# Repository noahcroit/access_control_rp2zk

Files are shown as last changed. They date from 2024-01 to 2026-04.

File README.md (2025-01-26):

# Access Control Project
The project consists of <br>
- PCB design and the firmware of `Fail-Secure` door lock for the access control room. <br>
- Python worker of access control interface. This software will interract with the room management system later <br>

The project has 2 different version, v2023 and v2024.

## v2023 version
This version was focused on Proof-of-Concept and do a rapid prototype with both HW and SW. Micropython was used for the firmware development in RP2040 as for the Doorlock controller\
ZkTeco's access control was being used in this phase.

## v2024 version (the current ver.) 
PCB design with KiCAD for the doorlock controller. Hikvision's access control is being used in this phase instead of ZkTeco's.

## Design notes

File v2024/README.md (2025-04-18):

# FailSecureDoor_RP2 version 2 (2024)
The room consists of slider automatic door which needs the fail-secure bolt-lock system when outage occured. <br>
KiCAD is used for the controller board design (in `kicad`) and RPi Pico C SDK framework is used for the firmware development (in `firmware`). <br>
By the dafault, each door has the access control device `DS-K1T105AM` installed alongside. <br>
Our access control software will used the Software Worker (in `worker`) to interface with `DS-K1T105AM` via `ISAPI` and fail-secure board via MQTT. <br>
<br>
### Hardware Diagram
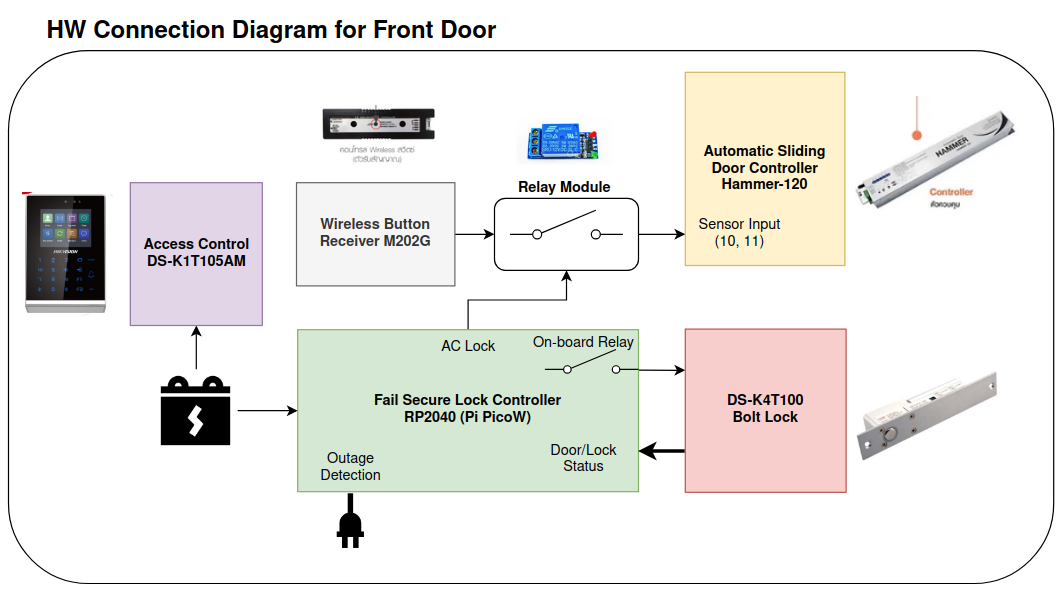
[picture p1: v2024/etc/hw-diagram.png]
 <br>
### Network Diagram
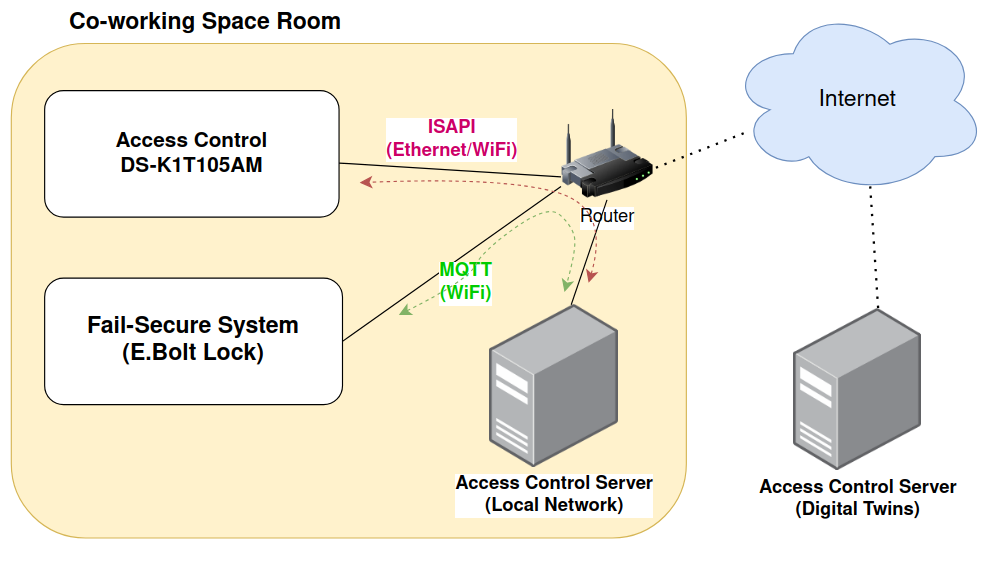
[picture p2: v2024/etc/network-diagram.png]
 <br>

### HW Installation
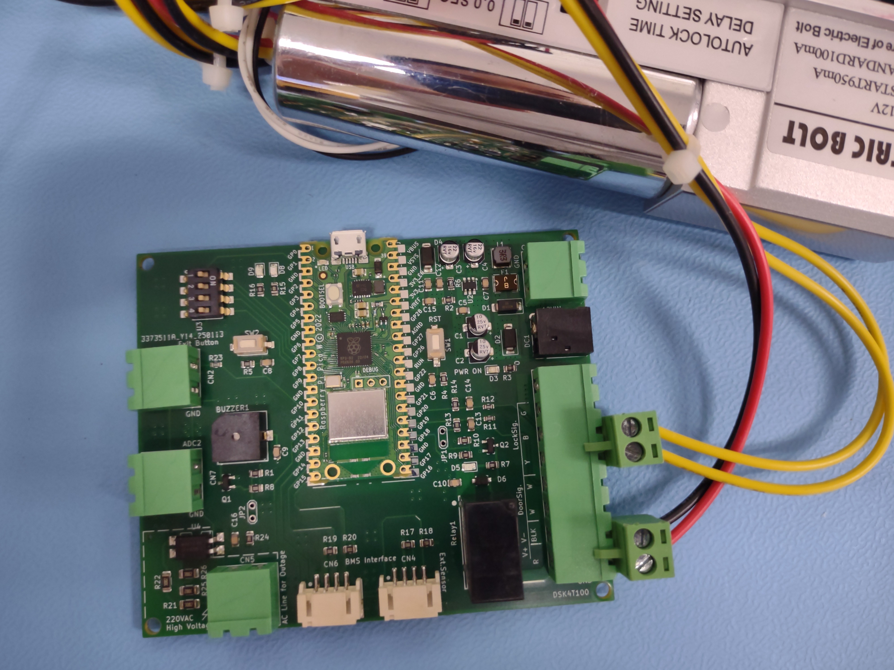
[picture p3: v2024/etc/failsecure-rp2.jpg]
 <br>
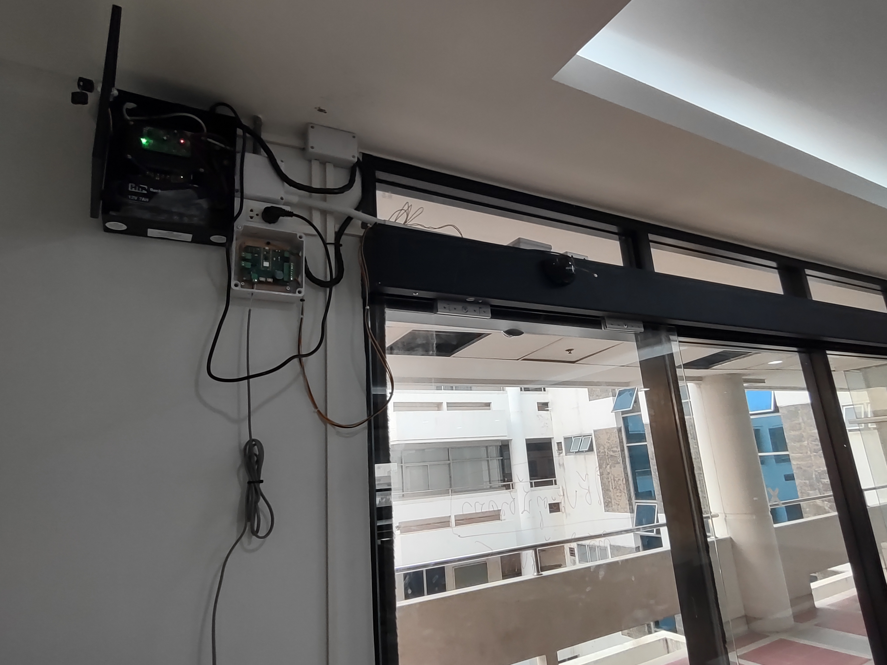
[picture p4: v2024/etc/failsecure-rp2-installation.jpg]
 <br>
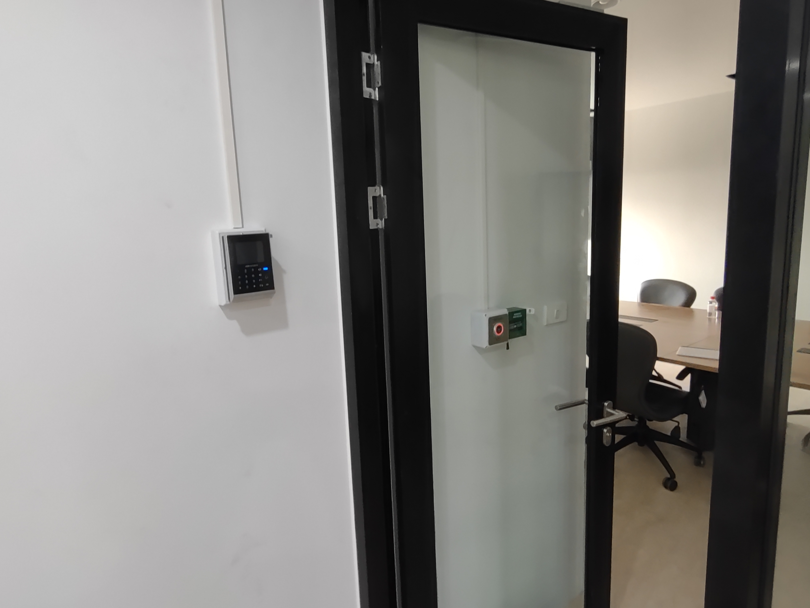
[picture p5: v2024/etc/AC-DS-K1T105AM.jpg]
 <br>

### Worker
To build the image <br>
```
cd worker
docker build -t acworker2024-image .
```

To run the worker as container <br>
```
docker run --network host -d --restart always --name acworker acworker2024-image
```

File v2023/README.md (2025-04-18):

# FailSecureDoor_RP2 version 1 (2023)
Firmware for Fail-secure door controller of access control room. It activates when power outage is occured. <br>
This is the rapid prototype project, PCB is constructed in a prototype way and Micropython are being used to develop the firmware. <br>
The access control unit is from ZkTeco brand. `pyzk` project is used for the python module to interface with ZkTeco AC. <br>
The project can be found in here https://github.com/fananimi/pyzk

### Fail-Secure Door Controller with Pico W (RP2040)
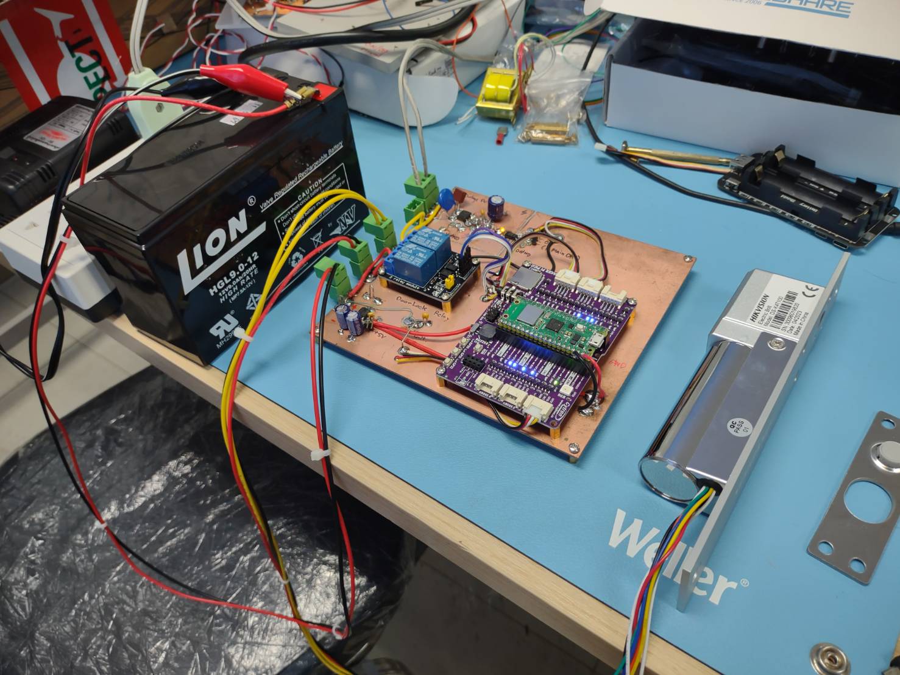
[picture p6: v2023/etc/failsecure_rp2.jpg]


The firmware is written in micropython, stored in folder `rp2`. `ampy` can be used to upload the codes to MCU.
To upload firmware.
1. Upload micropython firmware .uf2 of Pico W. The latest firmware can be founded in here
    https://micropython.org/download/RPI_PICO_W/
2. `cd` to the repo
```
cd access_control_rpzk
cd rp2
```
3. Run `ampy put` to put the network configuration .json file into MCU
```
ampy -p /dev/ttyACM0 network_config.json
```
4. Run `ampy put` to put the codes into MCU
```
ampy -p /dev/ttyACM0 put umqtt 
ampy -p /dev/ttyACM0 put main.py main.py q_scheduler.py secure_doorlock.py
```
5. Verify the upload files by `ampy ls` or `ampy get`
```
ampy -p /dev/ttyACM0 ls
```
6. Reset MCU and run it.

### Worker for ZKTeco's Access Control & FailSecure Door
To deploy using Docker
1. `cd` to the repo
```
cd access_control_rpzk
```
2. Build worker image
```
sudo docker build -t acworker-image .
```
3. Run container from built image
```
sudo docker run -d --network=host --name=acworker acworker-image
```

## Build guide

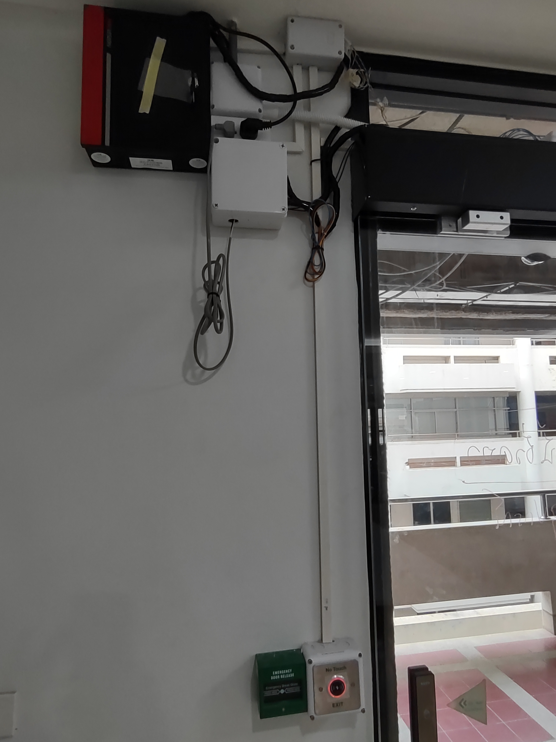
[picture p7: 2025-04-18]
v2024/etc/failsecure-rp2-installation-2.jpg

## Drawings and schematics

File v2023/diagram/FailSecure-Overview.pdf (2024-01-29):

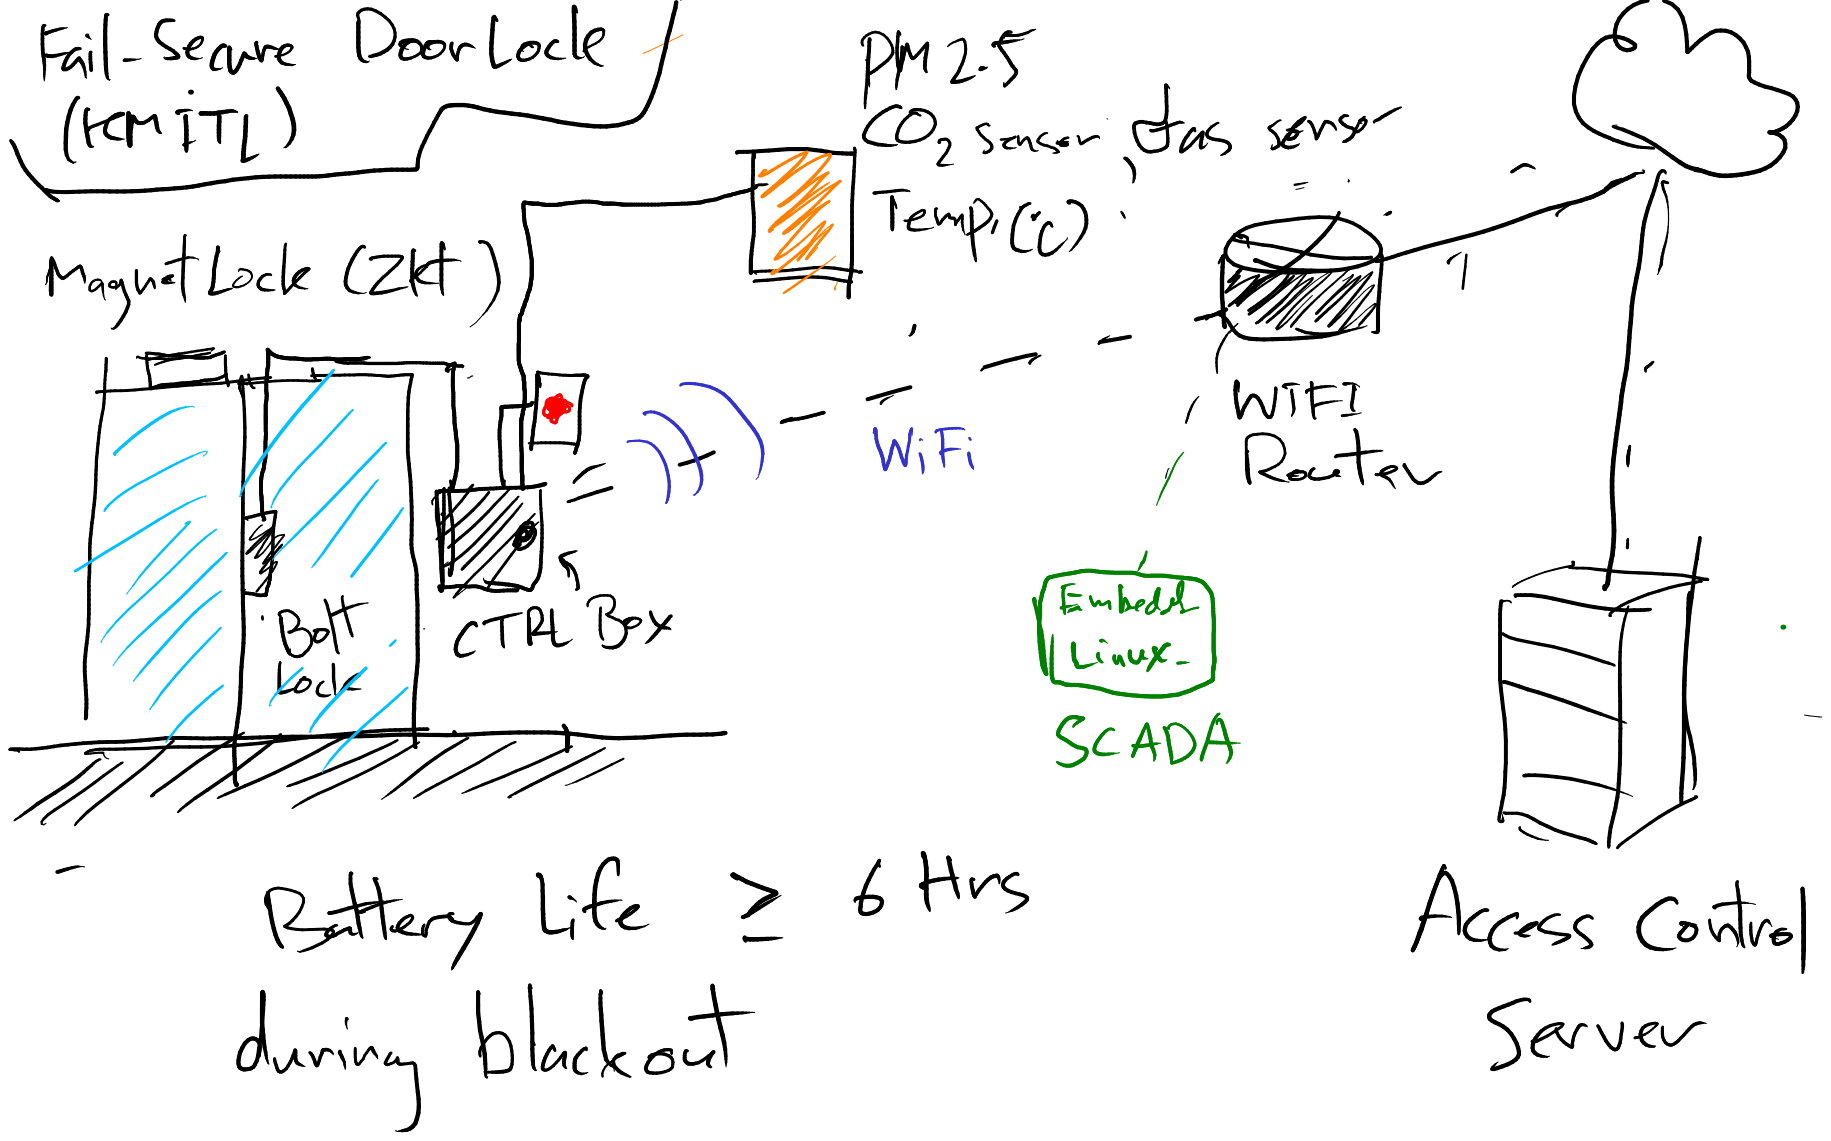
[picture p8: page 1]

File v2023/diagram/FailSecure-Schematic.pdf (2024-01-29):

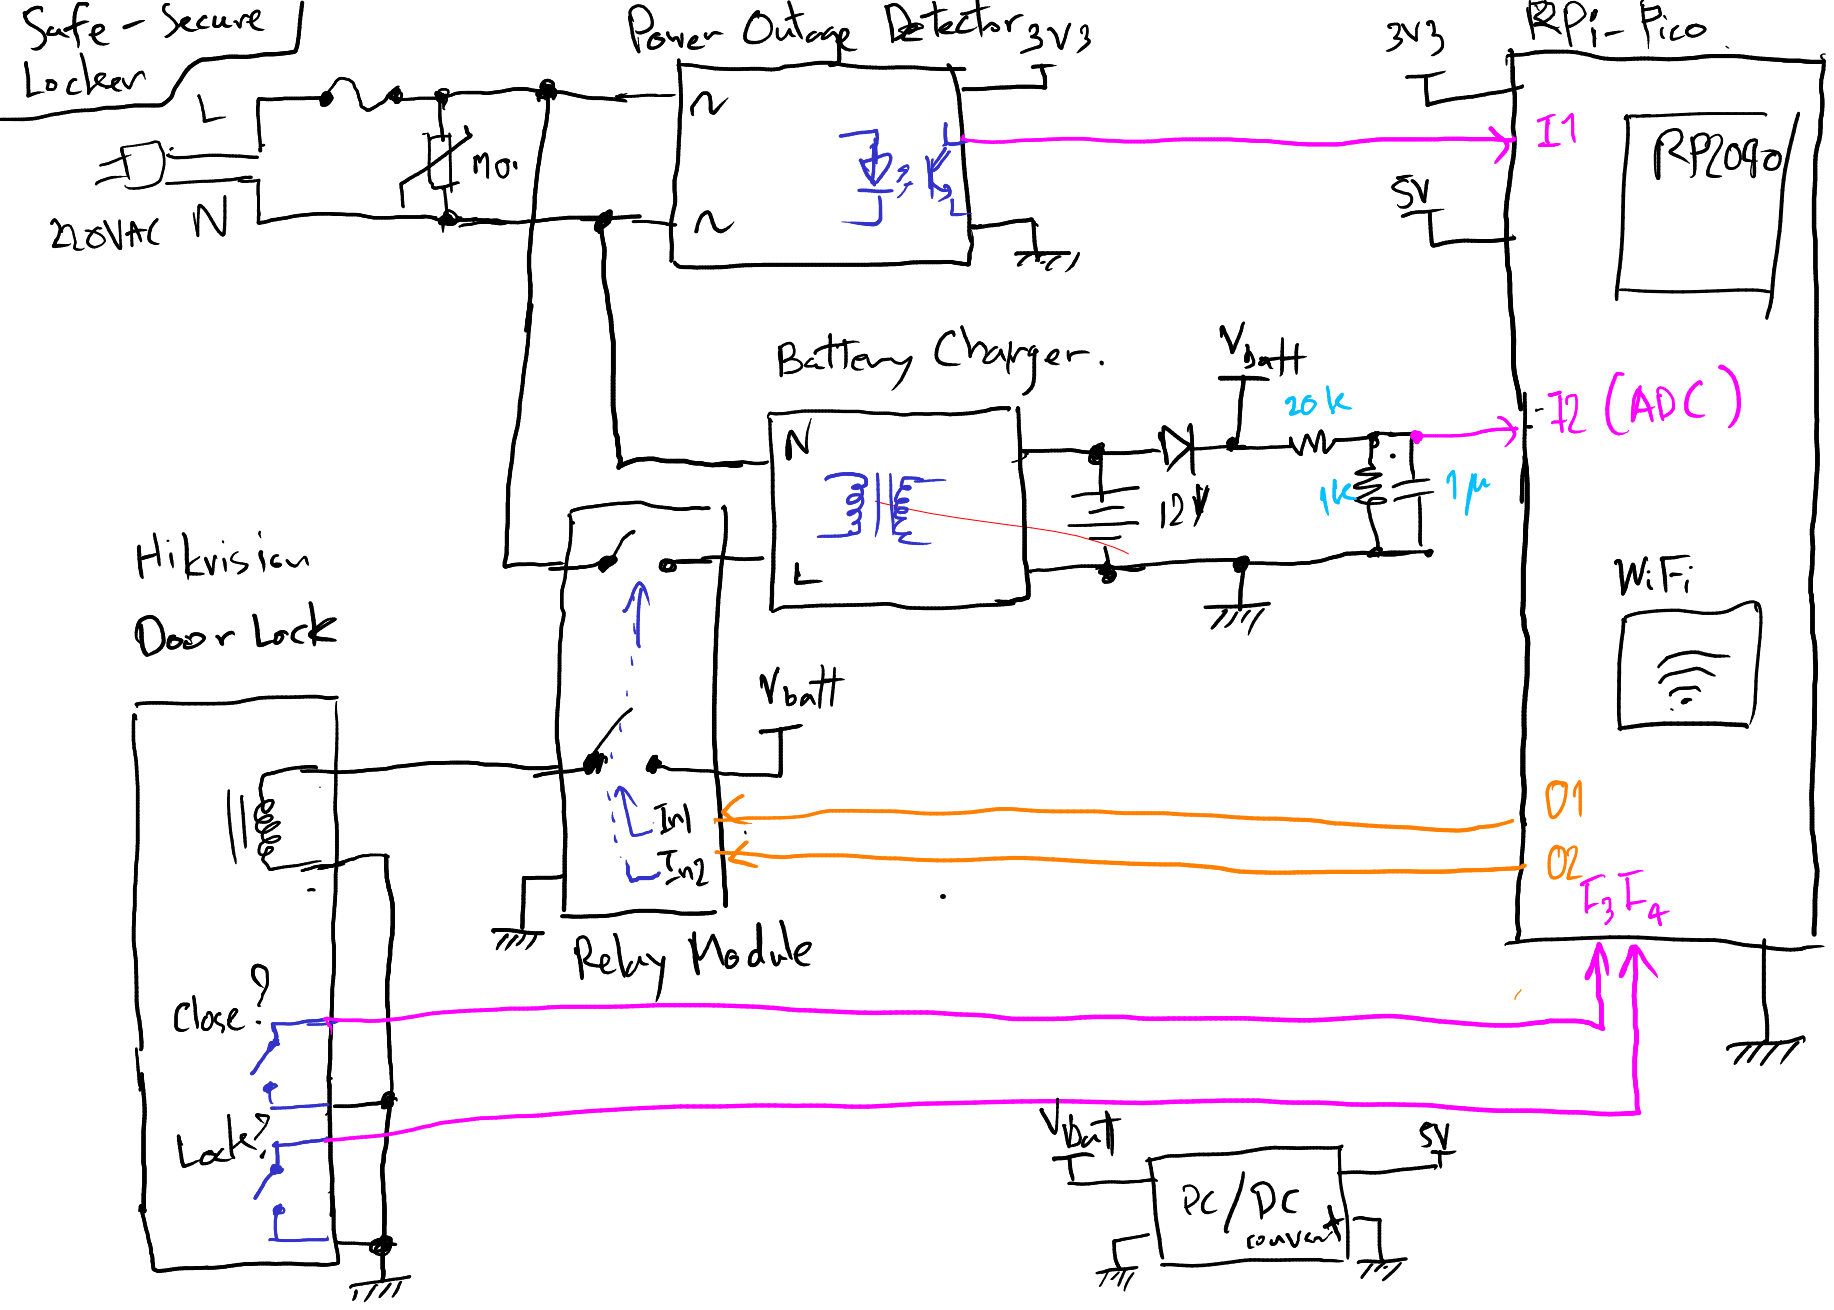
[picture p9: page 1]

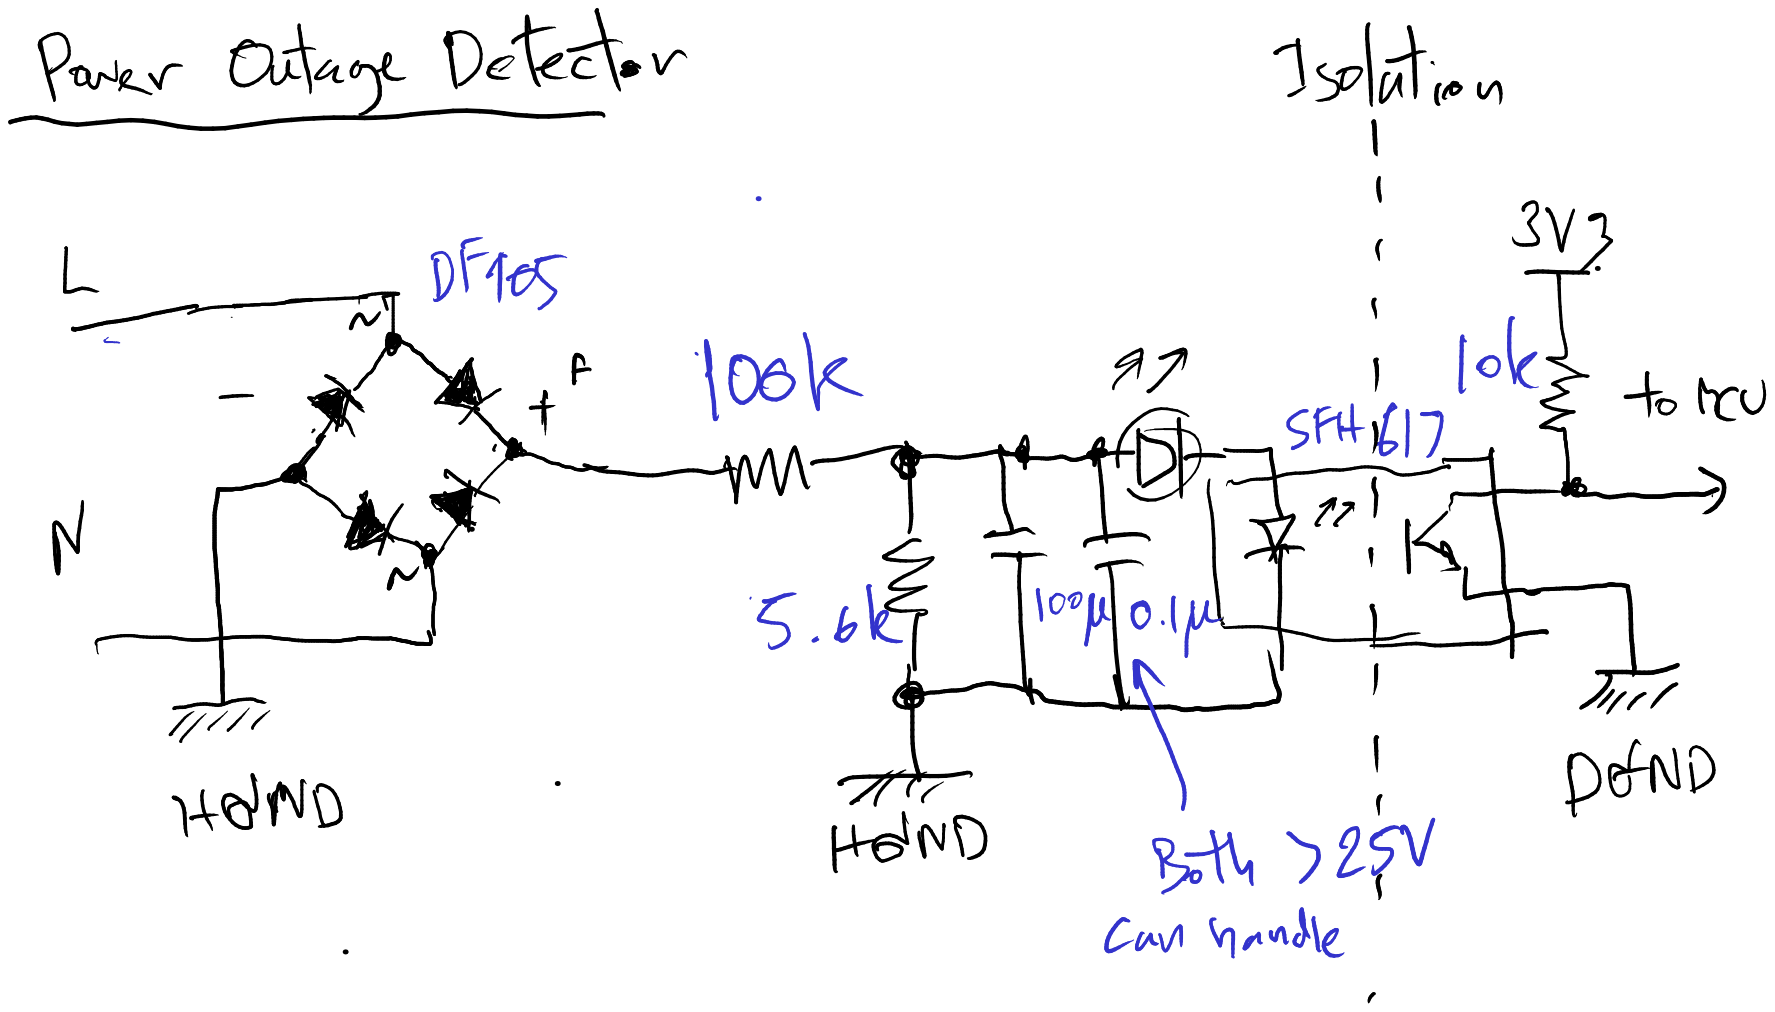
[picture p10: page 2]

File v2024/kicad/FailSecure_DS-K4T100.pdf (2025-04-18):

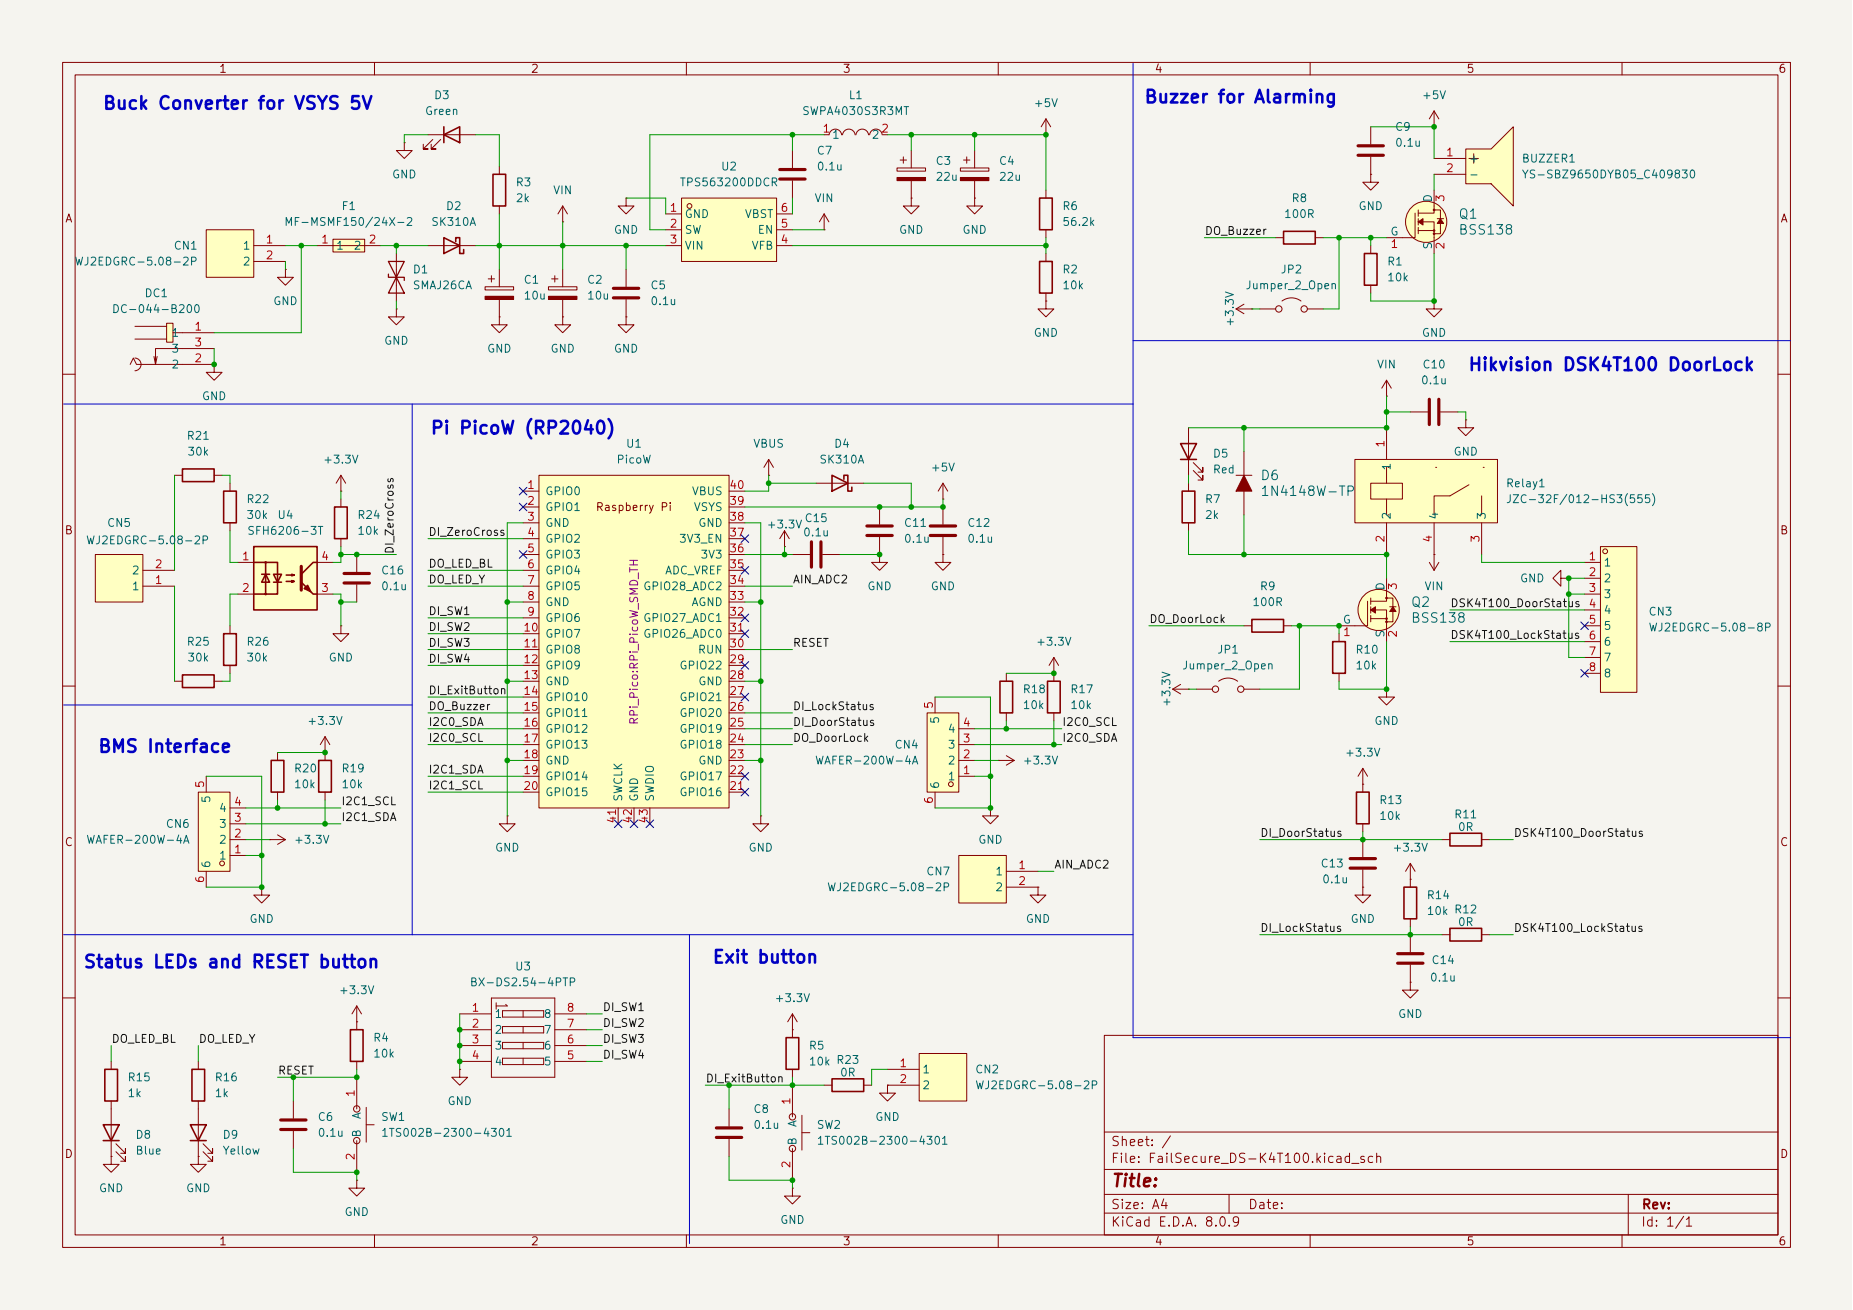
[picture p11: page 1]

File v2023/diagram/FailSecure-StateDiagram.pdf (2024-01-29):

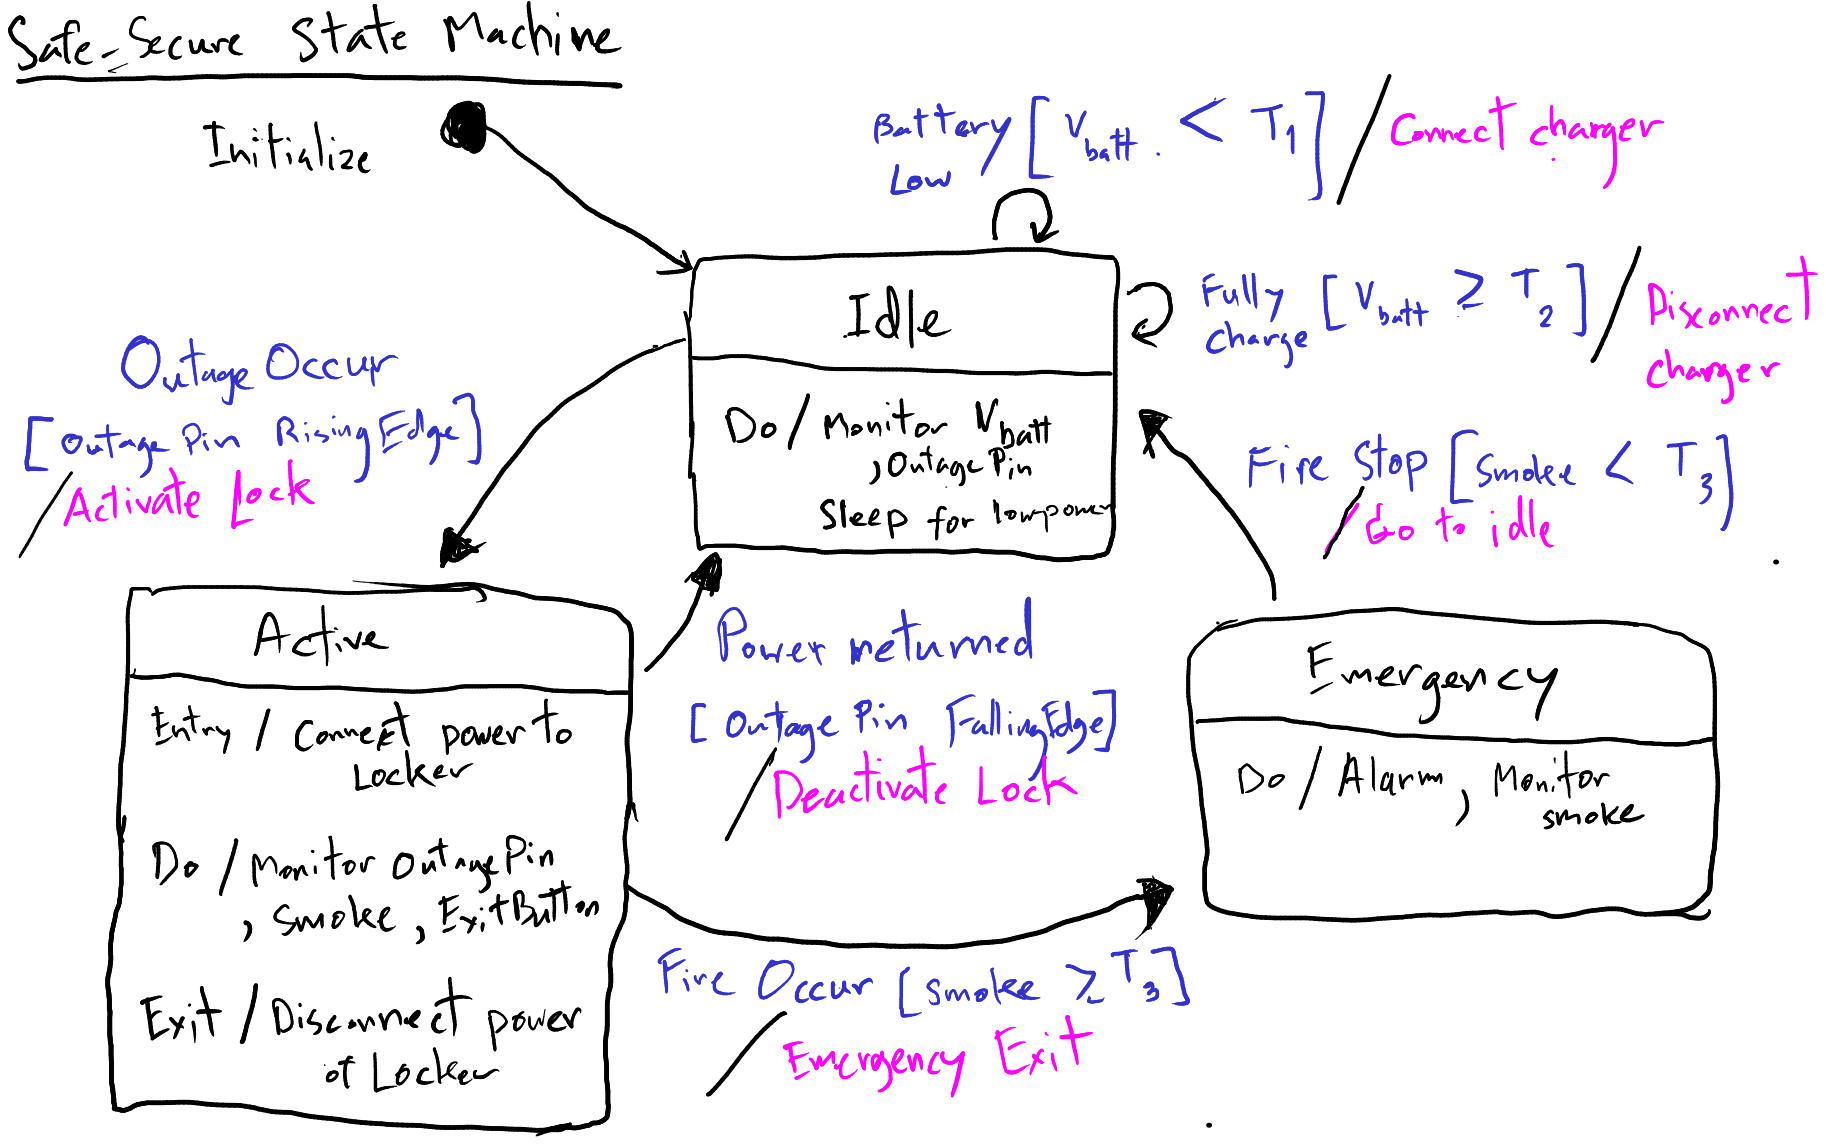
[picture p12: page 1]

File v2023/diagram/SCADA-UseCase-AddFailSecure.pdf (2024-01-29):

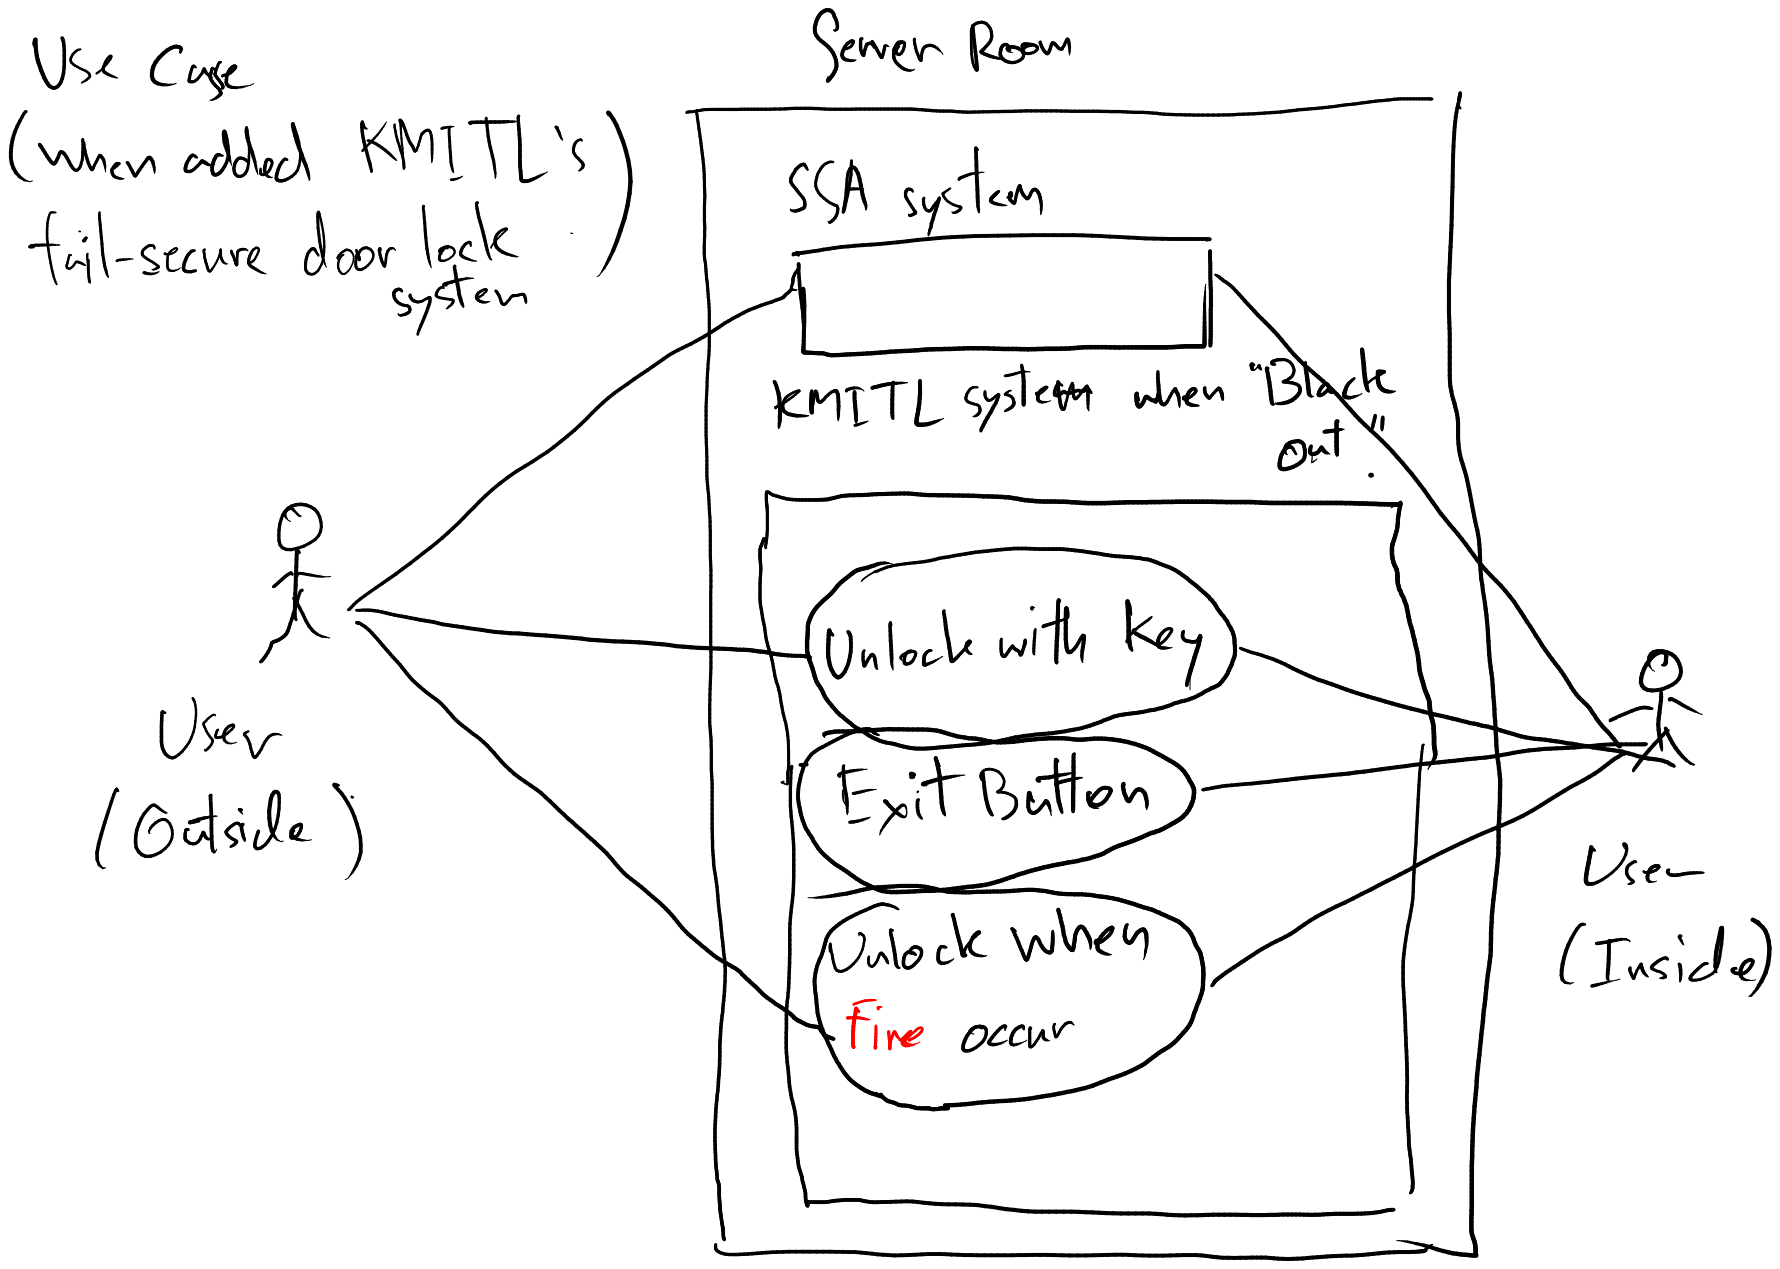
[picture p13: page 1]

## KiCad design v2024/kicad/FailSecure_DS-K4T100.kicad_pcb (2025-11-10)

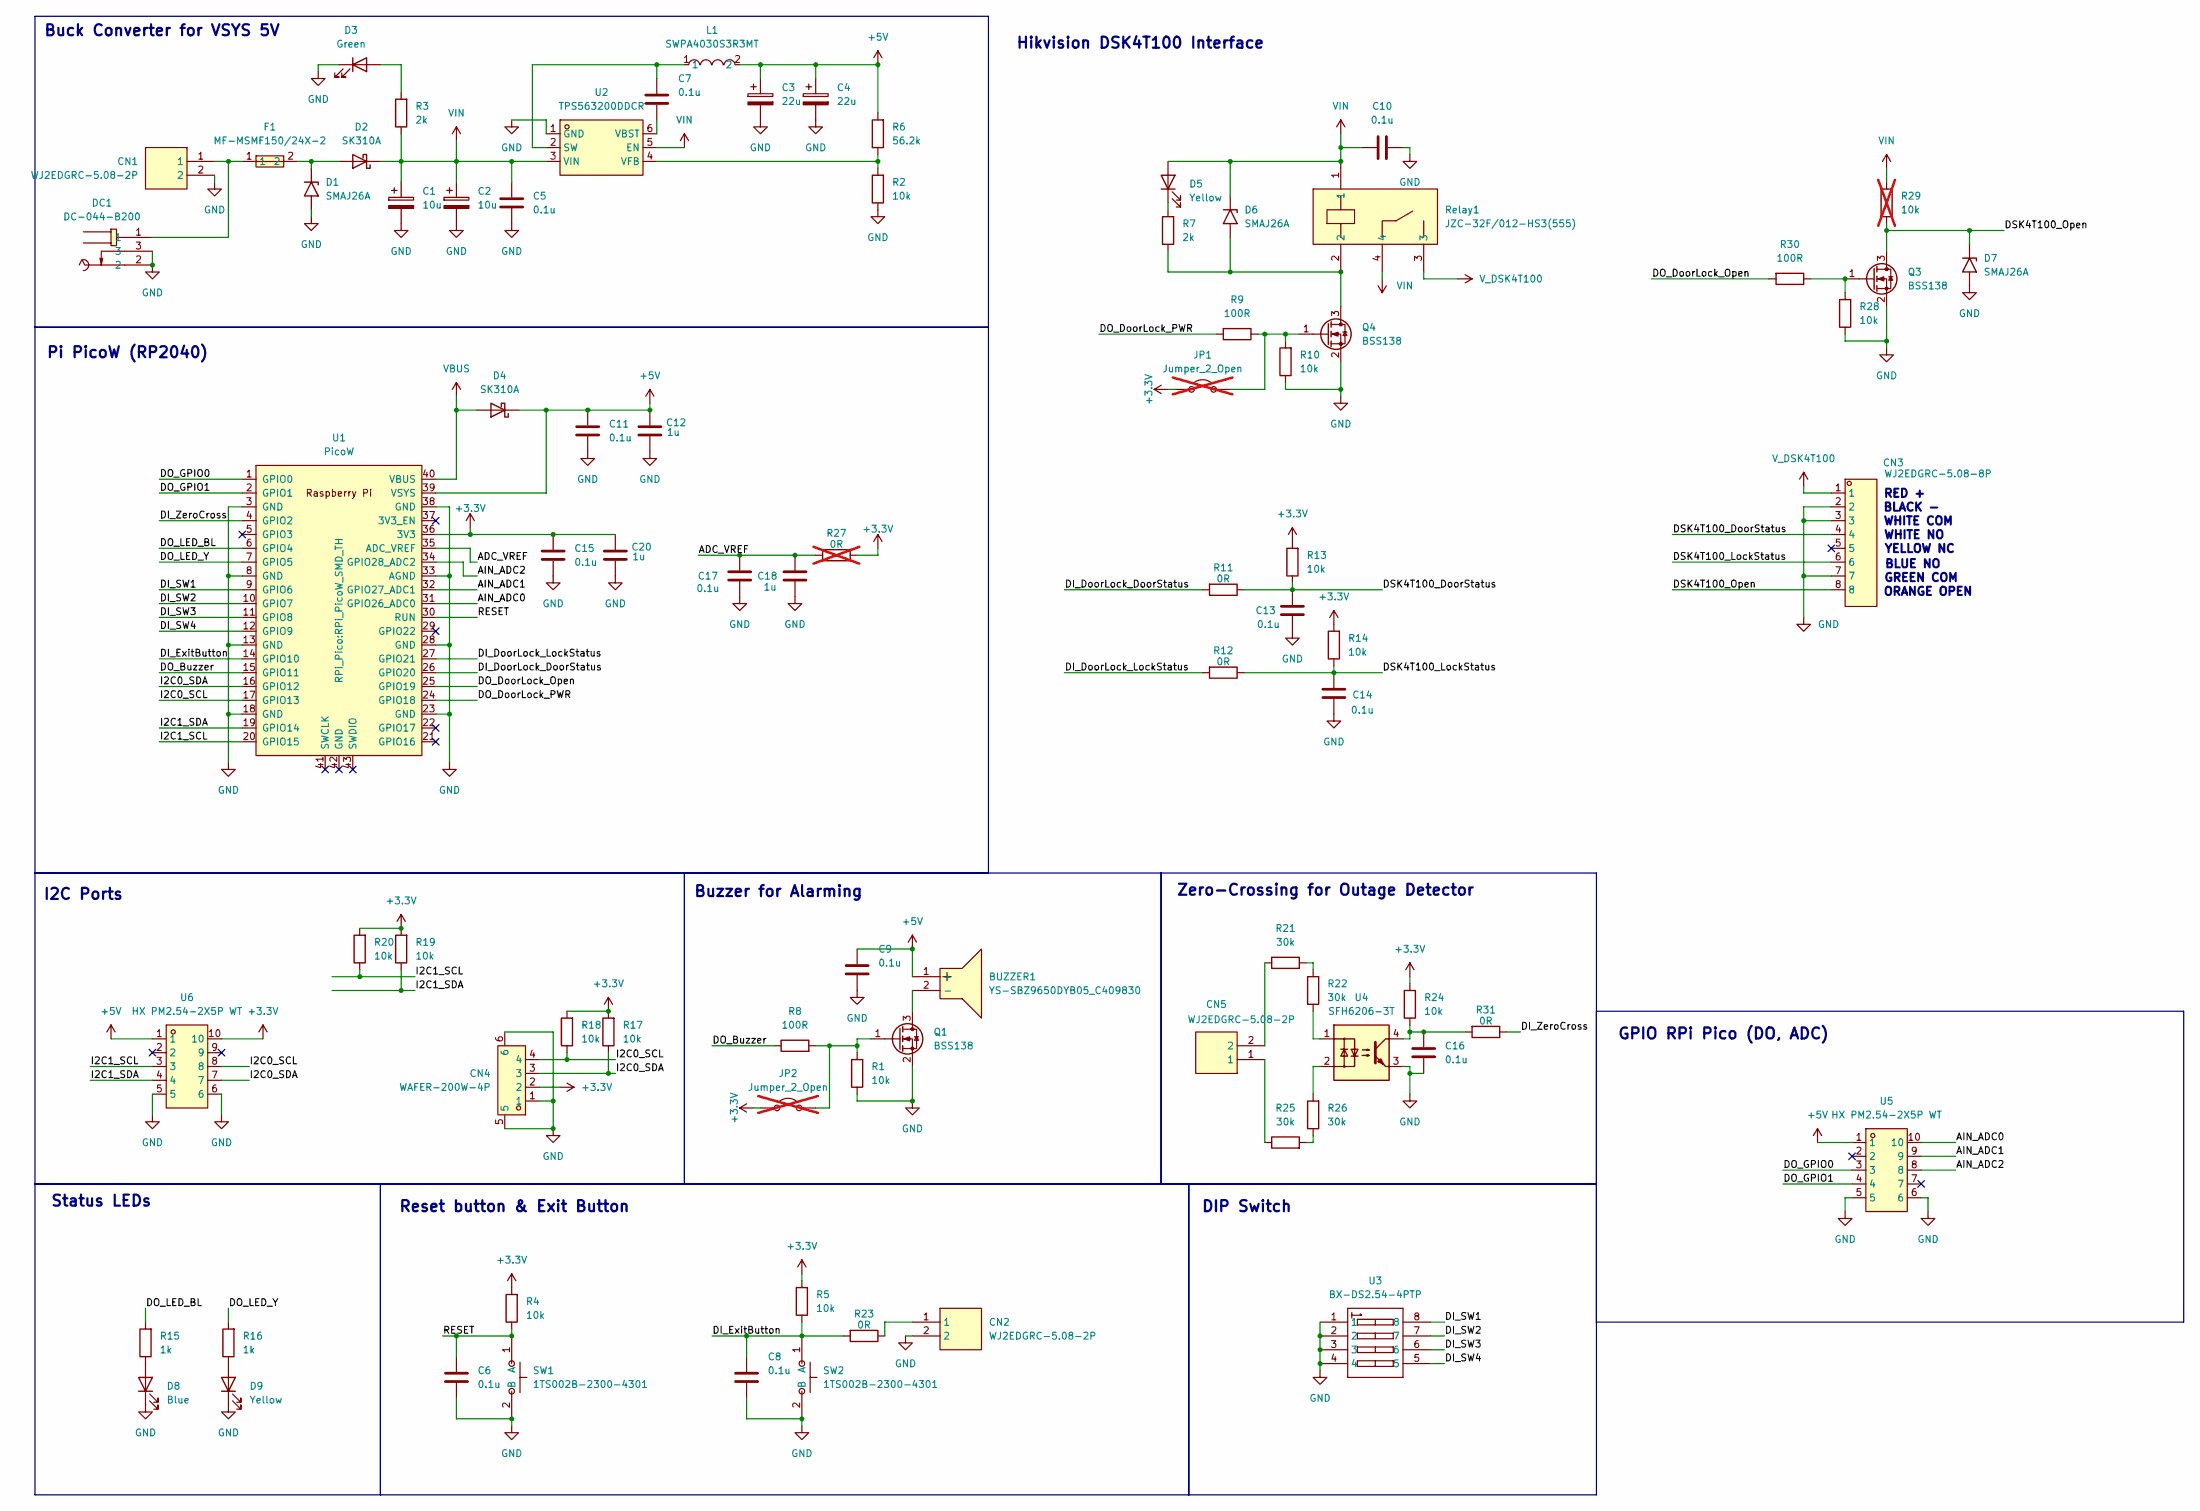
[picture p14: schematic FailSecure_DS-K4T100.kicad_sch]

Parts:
BUZZER1: YS-SBZ9650DYB05_C409830; BUZ-SMD_L9.6-W9.6-LS10.0-R; LCSC Part C409830
C1, C2: 10u; CP_Elec_4x5.4; LCSC Part C3343
C3, C4: 22u; CP_Elec_4x5.4; LCSC Part C3356
C5, C6, C7, C8, C9, C10, C11, C13, C14, C15, C16, C17: 0.1u; C_0805_2012Metric; Voltage 50V; Tolerance 100%; LCSC Part C138340
C12, C18, C20: 1u; C_1206_3216Metric; Voltage 50V; Tolerance 100%; LCSC Part C138340
CN1, CN2, CN5: WJ2EDGRC-5.08-2P; CONN-TH_2P-P5.08_WJ2EDGRC-5.08-2P; LCSC Part C3697
CN3: WJ2EDGRC-5.08-8P; CONN-TH_8P-P5.08_WJ2EDGRC-5.08-8P; LCSC Part C27587
CN4: WAFER-200W-4P; CONN-SMD_WAFER-200W-4P; LCSC Part C2840430
D1, D6, D7: SMAJ26A; D_SMA; LCSC Part C148225
D2, D4: SK310A; D_SMA; LCSC Part C91474
D3: Green; LED_0805_2012Metric; LCSC Part C2297
D5, D9: Yellow; LED_0805_2012Metric; LCSC Part C2296
D8: Blue; LED_0805_2012Metric; LCSC Part C2293
DC1: DC-044-B200; DC-IN-TH_DC-044-BXXX; LCSC Part C720573
F1: MF-MSMF150/24X-2; F1812; LCSC Part C78695
JP1, JP2: Jumper_2_Open; TestPoint_2Pads_Pitch2.54mm_Drill0.8mm; not fitted
L1: SWPA4030S3R3MT; IND-SMD_L4.0-W4.0_SMNR4012; LCSC Part C15269
Q1, Q3, Q4: BSS138; SOT-23-3; LCSC Part C431507
R1, R2, R4, R5, R10, R13, R14, R17, R18, R19, R20, R24, R28: 10k; R_0805_2012Metric; LCSC Part C17414
R3, R7: 2k; R_0805_2012Metric; LCSC Part C17604
R6: 56.2k; R_0805_2012Metric; LCSC Part C483186
R8, R9, R30: 100R; R_0805_2012Metric; LCSC Part C17408
R11, R12, R23, R31: 0R; R_0603_1608Metric; LCSC Part C21189
R15, R16: 1k; R_0805_2012Metric; LCSC Part C17513
R21, R22, R25, R26: 30k; R_1206_3216Metric; LCSC Part C17999
R27: 0R; R_0603_1608Metric; LCSC Part C304185; not fitted
R29: 10k; R_0805_2012Metric; LCSC Part C17414; not fitted
Relay1: JZC-32F/012-HS3(555); RELAY-TH_JZC-32F-012-HS3-555; LCSC Part C3632
SW1, SW2: 1TS002B-2300-4301; SW-SMD_L6.0-W3.5-LS8.0; LCSC Part C318833
U1: PicoW; RPi_PicoW_SMD_TH
U2: TPS563200DDCR; SOT-23-6_L2.9-W1.6-P0.95-LS2.8-BR; LCSC Part C97253
U3: BX-DS2.54-4PTP; SW-SMD_8P-L10.3-W6.2-P2.54-LS9.5-BL; LCSC Part C18078244
U4: SFH6206-3T; SMDIP-4_W9.53mm_Clearance8mm; LCSC Part C118295
U5, U6: HX PM2.54-2X5P WT; HDR-SMD_10P-P2.54-H-F-R2-C5-W8.5; LCSC Part C46635850

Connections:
+3.3V: C15.2, C20.1, CN4.2, JP1.1 (A), JP2.1 (A), R4.2, R5.2, R13.2, R14.2, R17.2, R18.2, R19.2, R20.2, R24.2, R27.1, U1.36 (3V3), U6.10
+5V: BUZZER1.1 (+), C3.1, C4.1, C9.1, C11.2, C12.1, D4.1 (K), L1.2, R6.2, U1.39 (VSYS), U5.1, U6.1
/ADC_VREF: C17.1, C18.1, R27.2, U1.35 (ADC_VREF)
/AIN_ADC0: U1.31 (GPIO26_ADC0), U5.10
/AIN_ADC1: U1.32 (GPIO27_ADC1), U5.9
/AIN_ADC2: U1.34 (GPIO28_ADC2), U5.8
/DI_DoorLock_DoorStatus: R11.2, U1.26 (GPIO20)
/DI_DoorLock_LockStatus: R12.2, U1.27 (GPIO21)
/DI_ExitButton: C8.1, R5.1, R23.2, SW2.1 (A), U1.14 (GPIO10)
/DI_SW1: U1.9 (GPIO6), U3.8
/DI_SW2: U1.10 (GPIO7), U3.7
/DI_SW3: U1.11 (GPIO8), U3.6
/DI_SW4: U1.12 (GPIO9), U3.5
/DI_ZeroCross: R31.1, U1.4 (GPIO2)
/DO_Buzzer: R8.1, U1.15 (GPIO11)
/DO_DoorLock_Open: R30.2, U1.25 (GPIO19)
/DO_DoorLock_PWR: R9.2, U1.24 (GPIO18)
/DO_GPIO0: U1.1 (GPIO0), U5.3
/DO_GPIO1: U1.2 (GPIO1), U5.4
/DO_LED_BL: R15.2, U1.6 (GPIO4)
/DO_LED_Y: R16.2, U1.7 (GPIO5)
/DSK4T100_DoorStatus: C13.2, CN3.4, R11.1, R13.1
/DSK4T100_LockStatus: C14.2, CN3.6, R12.1, R14.1
/DSK4T100_Open: CN3.8, D7.1 (A1), Q3.3 (D), R29.1
/I2C0_SCL: CN4.4, R18.1, U1.17 (GPIO13), U6.8
/I2C0_SDA: CN4.3, R17.1, U1.16 (GPIO12), U6.7
/I2C1_SCL: R20.1, U1.20 (GPIO15), U6.3
/I2C1_SDA: R19.1, U1.19 (GPIO14), U6.4
/RESET: C6.1, R4.1, SW1.1 (A), U1.30 (RUN)
GND: C1.2, C2.2, C3.2, C4.2, C5.1, C6.2, C8.2, C9.2, C10.2, C11.1, C12.2, C13.1, C14.1, C15.1, C16.1, C17.2, C18.2, C20.2, CN1.2, CN2.2, CN3.2, CN3.3, CN3.7, CN4.1, CN4.5, CN4.6, D1.2 (A2), D3.1 (K), D7.2 (A2), D8.1 (K), D9.1 (K), DC1.2, DC1.3, Q1.2 (S), Q3.2 (S), Q4.2 (S), R1.1, R2.1, R10.1, R28.1, SW1.2 (B), SW2.2 (B), U1.3 (GND), U1.8 (GND), U1.13 (GND), U1.18 (GND), U1.23 (GND), U1.28 (GND), U1.33 (AGND), U1.38 (GND), U2.1 (GND), U3.1, U3.2, U3.3, U3.4, U4.3, U5.5, U5.6, U6.5, U6.6
unnamed: BUZZER1.2 (-), Q1.3 (D)
unnamed: C16.2, R24.1, R31.2, U4.4
unnamed: CN1.1, DC1.1, F1.1
unnamed: CN2.1, R23.1
unnamed: CN5.1, R25.1
unnamed: CN5.2, R21.1
unnamed: D1.1 (A1), D2.2 (A), F1.2
unnamed: D3.2 (A), R3.2
unnamed: D5.1 (K), R7.2
unnamed: D6.2 (A2), Q4.3 (D), R7.1, Relay1.2
unnamed: D8.2 (A), R15.1
unnamed: D9.2 (A), R16.1
unnamed: JP1.2 (B), Q4.1 (G), R9.1, R10.2
unnamed: JP2.2 (B), Q1.1 (G), R1.2, R8.2
unnamed: Q3.1 (G), R28.2, R30.1
unnamed: R21.2, R22.1
unnamed: R22.2, U4.1
unnamed: R25.2, R26.1
unnamed: R26.2, U4.2
unnamed: C7.1, L1.1, U2.2 (SW)
unnamed: C7.2, U2.6 (VBST)
unnamed: R2.2, R6.1, U2.4 (VFB)
VBUS: D4.2 (A), U1.40 (VBUS)
VIN: C1.1, C2.1, C5.2, C10.1, D2.1 (K), D5.2 (A), D6.1 (A1), R3.1, R29.2, Relay1.1, Relay1.4, U2.3 (VIN), U2.5 (EN)
V_DSK4T100: CN3.1, Relay1.3

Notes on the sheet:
Zero-Crossing for Outage Detector
GPIO RPi Pico (DO, ADC)
Pi PicoW (RP2040)
GREEN COM
Status LEDs
BLACK -
WHITE NO
ORANGE OPEN
WHITE COM
Buzzer for Alarming
Reset button & Exit Button
RED +
DIP Switch
Buck Converter for VSYS 5V
BLUE NO
I2C Ports
Hikvision DSK4T100 Interface
YELLOW NC

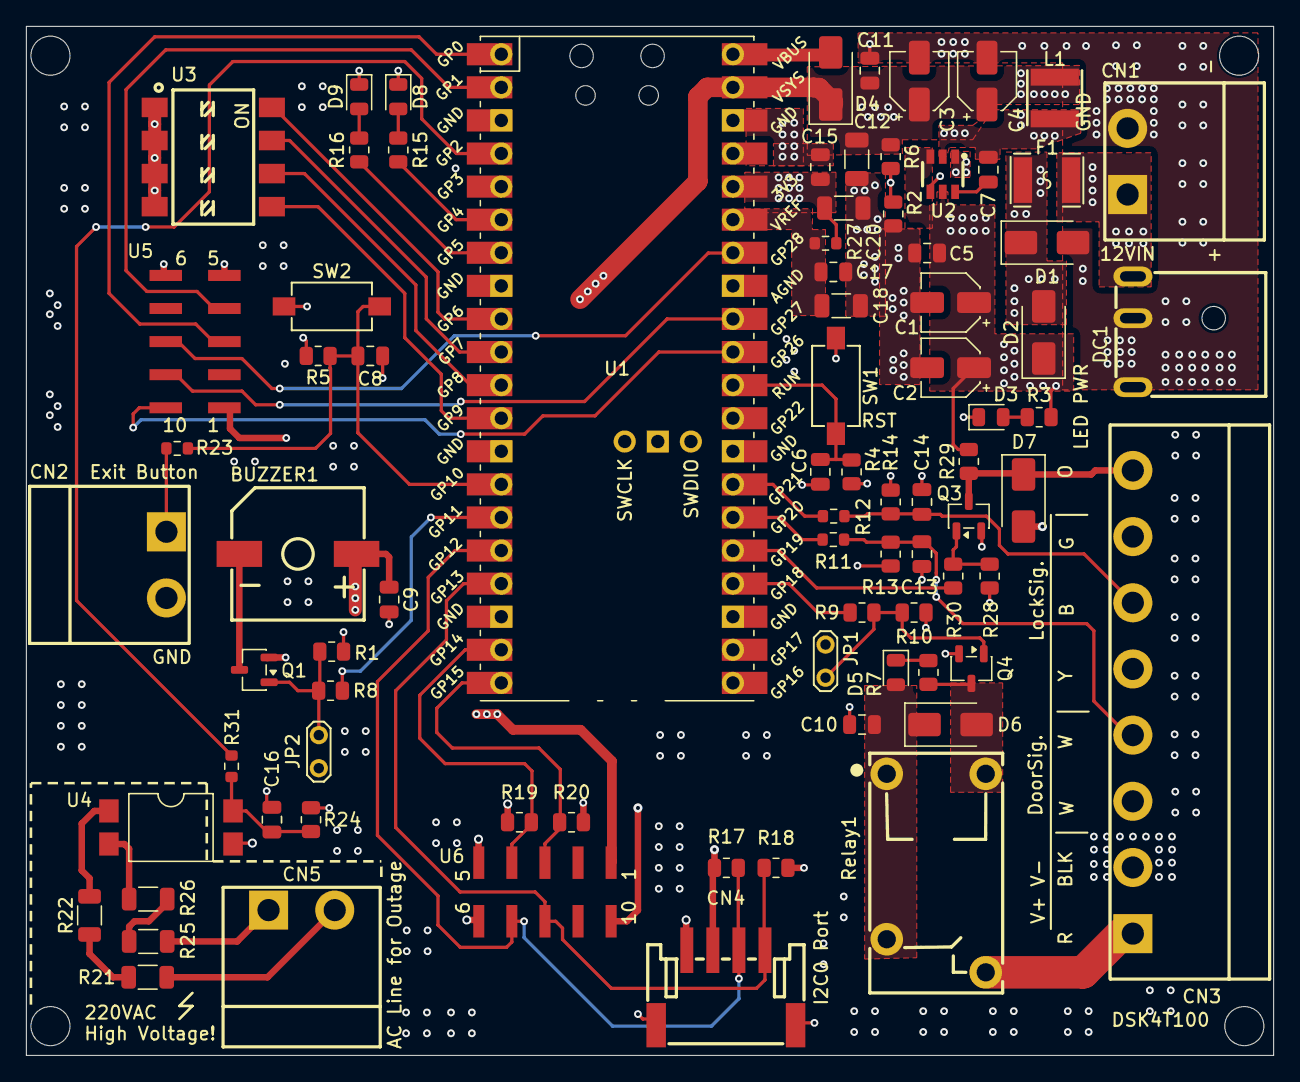
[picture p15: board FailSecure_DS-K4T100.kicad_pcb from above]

Board: 4 copper layers, 95.8 x 79.0 mm, 82 parts (0 on the bottom side), 55 nets.

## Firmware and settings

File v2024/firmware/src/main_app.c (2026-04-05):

#include <stdio.h>
#include <string.h>
#include "board_driver_rp2.h"
#include "app_button.h"
#include "app_led.h"
#include "app_buzzer.h"
#include "app_dsk4t100.h"
#include "app_outage.h"
#include "app_accessctrl.h"

#define USE_WIFI 0

#if USE_WIFI == 1
#include "app_mqtt.h"
#endif

#define PERIOD_GLOBAL_TICK_MS (uint32_t)1000
#define STATE_IDLE 1
#define STATE_ACTIVE 2  // when outage occured, fail-secure activates
#define EXIT_DELAY_STARTVALUE 15
#define EXIT_OUTAGE_DELAY_STARTVALUE 30
#define DIPSWITCH_MODE_SILENT_BUZZER 1
#define WATCHDOG_TIME_MS (uint32_t)5000

/*
 * Callback functions for apps 
 *
 */
void on_button_pressed_onboard();
void on_button_pressed_exit();
#if USE_WIFI == 1
void on_mqtt_connection(mqtt_client_t* client, void* arg, mqtt_connection_status_t status);
void on_mqtt_sub_request(void *arg, err_t err);
void on_mqtt_incoming_publish(void *arg, const char *topic, u32_t tot_len);
void on_mqtt_incoming_data(void *arg, const u8_t *data, u16_t len, u8_t flags);
void on_mqtt_pub_request(void *arg, err_t result);
/*
 * MQTT functions for apps. It can't be wrapped in app-layer (app_mqtt.c) because of IwIP doesn't allow to.
 *
 */
void app_mqtt_connect(mqtt_client_t* client);
void app_mqtt_publish(mqtt_client_t *client, const char *pub_topic, char *pub_payload);
#endif

/*
 * Struct for all devices
 *
 */
app_button_t button = {
    .driver_read_gpio = driver_rp2_read_gpio,
    .driver_set_gpio_input = driver_rp2_set_gpio_input,
    .driver_enable_gpio_global_interrupt = driver_rp2_enable_gpio_global_interrupt,
    .driver_set_gpio_callback = driver_rp2_set_gpio_callback,
    .cb_exit = on_button_pressed_exit,
    .gpio_num_exit_button = DI_EXITBUTTON,
    .gpio_num_dipsw1 = DI_SW1,
    .gpio_num_dipsw2 = DI_SW2,
    .gpio_num_dipsw3 = DI_SW3,
    .gpio_num_dipsw4 = DI_SW4
};

app_led_t led = {
    .driver_write_gpio = driver_rp2_write_gpio,
    .driver_set_gpio_output = driver_rp2_set_gpio_output,
    .gpio_num_led_y = DO_LED_Y,
    .gpio_num_led_b = DO_LED_B
};

app_buzzer_t buzzer = {
    .driver_write_gpio = driver_rp2_write_gpio,
    .driver_set_gpio_output = driver_rp2_set_gpio_output,
    .gpio_num = DO_BUZZER
};

app_dsk4t100_t locker = {
    .driver_read_gpio = driver_rp2_read_gpio,
    .driver_write_gpio = driver_rp2_write_gpio,
    .driver_set_gpio_input = driver_rp2_set_gpio_input,
    .driver_set_gpio_output = driver_rp2_set_gpio_output,
    .gpio_num_lockctrl = DO_DOORLOCK,
    .gpio_num_lockstatus = DI_LOCKSTATUS,
    .gpio_num_doorstatus = DI_DOORSTATUS
};

app_outage_t outage = {
    .driver_read_gpio = driver_rp2_read_gpio,
    .driver_set_gpio_input = driver_rp2_set_gpio_input,
    .driver_enable_gpio_global_interrupt = driver_rp2_enable_gpio_global_interrupt,
    .driver_set_gpio_callback = driver_rp2_set_gpio_callback,
    .gpio_num = DI_ZEROCROSS,
    .threshold = THRESHOLD_COUNT_OUTAGE
};

app_accessctrl_t ac = {
    .driver_write_gpio = driver_rp2_write_gpio,
    .driver_set_gpio_output = driver_rp2_set_gpio_output,
    .gpio_num_slidedoor = DO_ACCESSCTRLLOCK,
    .lockstate = false,
    .lockrequested = false,
    .unlockrequested = false
};

#if USE_WIFI == 1
mqtt_client_t* mqttc_lwip;
const char *WIFI_SSID = "";
const char *WIFI_PWD = "";
const int WIFI_CONNECTING_TIMEOUT_MS = 10000;
const char *USER_MQTT_BROKER = "192.168.8.102";
const int USER_MQTT_PORT = 1883;
const char *MQTT_TOPIC_ISOPENED = "door1/isopened";
const char *MQTT_TOPIC_ISLOCKED = "door1/islocked";
const char *MQTT_TOPIC_LOCKCTRL = "door1/lockctrl";
const char *MQTT_CLIENT_ID = "picow1";
const int MQTT_PUBLISH_PERIOD_SEC = 60; 
app_mqtt_status_t mqtt = {
    .state = MQTT_STATE_NOT_CONNECTED,
    .isconnected = false
};
#endif

uint8_t state=STATE_IDLE;
bool flag_exit_button=false;
uint8_t incoming_message_id=0;
const uint8_t MESSAGE_ID_TOPIC_LOCKCTRL = 1;
const uint8_t MESSAGE_ID_TOPIC_OTHERS = 0;


/*
 * main loop
 *
 */
int main() {
    // system initalize
    driver_rp2_sysinit();
    driver_rp2_create_global_tick(PERIOD_GLOBAL_TICK_MS);

    // App initialize
    app_button_init(&button);
    app_led_init(&led);
    app_buzzer_init(&buzzer);
    app_dsk4t100_init(&locker);
    app_accessctrl_init(&ac);
    app_outage_init(&outage);

#if USE_WIFI == 1
    // WiFi initialize
    driver_rp2_enable_wifi();
    driver_rp2_connect_to_wifi(WIFI_SSID,
                                WIFI_PWD, 
                                WIFI_CONNECTING_TIMEOUT_MS
                                );
    
    // MQTT client initialize
    mqttc_lwip = mqtt_client_new();
#endif
    
    // Enable watchdog
    driver_rp2_watchdog_enable(WATCHDOG_TIME_MS);
    
    uint8_t exit_cnt=0;
    uint32_t current_tick=0;
    uint32_t tick_previous_pub=0;
    while (1){
        current_tick = driver_rp2_get_global_tick();
        driver_sleep_ms(100);
        switch (state) {
            case STATE_IDLE:
                // task : monitor an outage event
                if(app_is_outage_occured(&outage)) {
                    app_led_y_on(&led);
                    app_dsk4t100_lock(&locker);
                    if (app_read_dipswitch(&button) !=  DIPSWITCH_MODE_SILENT_BUZZER) {
                        app_buzzer_on(&buzzer);
                    }
                    flag_exit_button = false;
                    state = STATE_ACTIVE;
                    break;
                }
                else {
                    app_dsk4t100_unlock(&locker);
                }

#if USE_WIFI == 1
                // task : WiFi & MQTT connection
                if(driver_rp2_is_wifi_connected()) {
                    if(!mqtt.isconnected) {
                        app_led_b_off(&led);
                        // run connect only 1 time when in MQTT disconnected state
                        if(mqtt.state != MQTT_STATE_CONNECTING) {
                            app_mqtt_connect(mqttc_lwip);
                            mqtt.state = MQTT_STATE_CONNECTING;
                        }
                    }
                    else{
                        app_led_b_on(&led);
                        // MQTT publish routine for device status
                        uint32_t diff;
                        if(current_tick >= tick_previous_pub) {
                            diff = current_tick - tick_previous_pub;
                        }
                        else {
                            diff = (0xffffffff - tick_previous_pub) + current_tick + 1;
                        }
                        if(diff >= MQTT_PUBLISH_PERIOD_SEC) {
                            // publish cmd
                            char payload[2] = "N";
                            if(app_dsk4t100_is_open(&locker)) payload[0] = 'Y';
                            else payload[0] = 'N';
                            app_mqtt_publish(mqttc_lwip, MQTT_TOPIC_ISOPENED, payload);
                            // update task's tick
                            tick_previous_pub = current_tick;
                        }
                    }
                }
                else{
                    app_led_b_off(&led);
                    // reconnecting the WIFI
                    driver_rp2_connect_to_wifi(WIFI_SSID,
                                                WIFI_PWD,
                                                WIFI_CONNECTING_TIMEOUT_MS
                                                );
                }
#endif

                // task : check slidedoor exit request from Exit Button
                if(flag_exit_button) {
                    app_accessctrl_open(&ac);
                    exit_cnt = EXIT_DELAY_STARTVALUE;
                    flag_exit_button = false;
                }
                if(exit_cnt > 0) {
                    exit_cnt--;
                    if(exit_cnt == 0) {
                        app_accessctrl_close(&ac);
                    }
                }
                break;

            case STATE_ACTIVE:
                // task : monitor EXIT button
                if(flag_exit_button) {
                    app_dsk4t100_unlock(&locker);
                    exit_cnt = EXIT_OUTAGE_DELAY_STARTVALUE;
                    flag_exit_button = false;
                }
                if(exit_cnt > 0) {
                    exit_cnt--;
                    if(exit_cnt == 0) {
                        app_dsk4t100_lock(&locker);
                    }
                }
                // task : monitor outage, if power is returned or not.
                if(!app_is_outage_occured(&outage)) {
                    app_led_y_off(&led);
                    app_dsk4t100_unlock(&locker);
                    app_buzzer_off(&buzzer);
                    app_accessctrl_close(&ac);
                    state = STATE_IDLE;
                }
                break;
        } // End-of-Switch
        
        // watchdog feed
        driver_rp2_watchdog_feed();
    }
    return 0;
}



/*
 * Callback functions for apps
 *
 */
void on_button_pressed_exit(){
    driver_debug_print("Exit button is pressed!\n");
    flag_exit_button = true;
}

#if USE_WIFI == 1
void on_mqtt_connection(mqtt_client_t* client, void* arg, mqtt_connection_status_t status) {
    err_t err;
    driver_debug_print("cb is called!\n");
    if (status == MQTT_CONNECT_ACCEPTED) {
        driver_debug_print("mqtt_connection_cb: Successfully connected\n");
        mqtt.isconnected = true;
        mqtt.state = MQTT_STATE_CONNECTED;

        /*
         * Run subscribe after device is connected
         */
        mqtt_sub_unsub(client, MQTT_TOPIC_LOCKCTRL, 0, on_mqtt_sub_request, 0, 1);
        mqtt_set_inpub_callback(client, on_mqtt_incoming_publish, on_mqtt_incoming_data, 0);
    } 
    else {
        driver_debug_print("mqtt_connection_cb: Disconnected, reason: ");
        driver_debug_print_int(status);
        driver_debug_print("\n");
        mqtt.isconnected = false;
        mqtt.state = MQTT_STATE_NOT_CONNECTED;
    }
}

void on_mqtt_sub_request(void *arg, err_t err) {
    driver_debug_print("mqtt_sub_request_cb: err ");
    driver_debug_print_int(err);
    driver_debug_print("\n");
}

void on_mqtt_incoming_publish(void *arg, const char *topic, u32_t tot_len) {
    driver_debug_print("Incoming publish at topic ");
    driver_debug_print(topic);
    driver_debug_print("\n");

    if(!strcmp(topic, MQTT_TOPIC_LOCKCTRL)) {
        incoming_message_id = MESSAGE_ID_TOPIC_LOCKCTRL;
    }
    else{
        incoming_message_id = MESSAGE_ID_TOPIC_OTHERS;
    }
}

void on_mqtt_incoming_data(void *arg, const u8_t *data, u16_t len, u8_t flags) {
    // create payload from incoming data
    char *payload = (char *)malloc(len + 1);
    memcpy(payload, data, len * sizeof(char));
    payload[len] = '\0';
    driver_debug_print("Incoming publish payload with len=");
    driver_debug_print_int(len);
    driver_debug_print(", flag=");
    driver_debug_print_int((unsigned int)flags);
    driver_debug_print("\nMQTT payload: ");
    driver_debug_print(payload);
    driver_debug_print("\n");
    
    if(incoming_message_id == MESSAGE_ID_TOPIC_LOCKCTRL) {
        if(!strcmp(payload, "ON"))       ac.lockrequested = true;
        else if(!strcmp(payload, "OFF")) ac.unlockrequested = true;
    }
    free(payload);
}

/* Called when publish is complete either with sucess or failure */
void on_mqtt_pub_request(void *arg, err_t result) {
    if(result != ERR_OK) {
        driver_debug_print("Publish result : ");
        driver_debug_print_int(result);
        driver_debug_print("\n");
    }
    else{
        driver_debug_print("cb, Publish OK\n");
    }
}

/*
 * MQTT functions
 *
 */
void app_mqtt_connect(mqtt_client_t* client) {
    struct mqtt_connect_client_info_t ci;
    err_t err;

    /* Setup an empty client info structure */
    memset(&ci, 0, sizeof(ci));

    /* Minimal amount of information required is client identifier, so set it here */
    ci.client_id = MQTT_CLIENT_ID;

    ip_addr_t mqtt_ip;
    ip4addr_aton(USER_MQTT_BROKER, &mqtt_ip);

    //cyw43_arch_lwip_begin();
    driver_debug_print("mqtt_client_connect()\n");
    err = mqtt_client_connect(mqttc_lwip, &mqtt_ip, USER_MQTT_PORT, on_mqtt_connection, 0, &ci);
    //cyw43_arch_lwip_end();

    /* For now just print the result code if something goes wrong*/
    driver_debug_print("ERR return : ");
    driver_debug_print_int(err);
    driver_debug_print("\n");
}

void app_mqtt_publish(mqtt_client_t *client, const char *pub_topic, char *pub_payload) {
    u8_t qos = 0; /* 0 1 or 2, see MQTT specification */
    u8_t retain = 0; /* No don't retain such crappy payload... */
    mqtt_publish(client, 
                pub_topic,
                pub_payload,
                strlen(pub_payload),
                qos,
                retain,
                on_mqtt_pub_request,
                NULL);
}
#endif

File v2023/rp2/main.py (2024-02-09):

import gc
from machine import Timer
from machine import WDT
from secure_doorlock import *
import time
import network
from umqtt.simple import MQTTClient
import ubinascii
from q_scheduler import FunctionQueueTask
from q_scheduler import FunctionQueueScheduler
import json



def mqttSubscribeCallback(topic, msg):
    global nc
    global door

    print("incoming MQTT message, ", (topic, msg))
    msg = msg.decode()
    if msg == "lock":
        door.lockEnable()
    elif msg == "unlock":
        door.lockDisable()



def task_displayAllDoorInfo():
    global door
    global door_dict

    door_dict["vbatt"] = str(door.getVbatt())
    door_dict["isopen"] = str(door.isDoorOpen())
    door_dict["ischarge"] = str(door.isChargerActivated())
    door_dict["state"] = str(door.state)
    print(door_dict)

def task_stepDoorState():
    global door
    door.step()

def task_mqttPublish():
    global door_dict
    global door
    global nc
    global wlan
    global mqtt_c
    global mqtt_connected
    global mqtt_client_id
    global wdt

    if not door.state == 'ACTIVE':
        # try to connect WLAN first
        timeout=0
        if not wlan.isconnected():
            try:
                print('connecting to WLAN...')
                wlan.active(True)
                wlan.connect(nc["ssid"],nc["pwd"])
                while not wlan.isconnected() and timeout < 20:
                    timeout += 1
                    time.sleep(0.1)
            except Exception as e:
                print(e)
                gc.collect()
                mqtt_connected = False

        # feed watchdog first to prevent reset itself due to long duration of connection
        wdt.feed()

        # do mqtt when WLAN is connected successfully
        # otherwise, wait for next call
        if wlan.isconnected():
            print("WLAN connected!")
            try:
                if not mqtt_connected:
                    mqtt_c.connect()
                    topic=nc["topics"][1].encode()
                    print('MQTT Subscribe to ', topic)
                    mqtt_c.subscribe(topic)

                topic=nc["topics"][0].encode()
                print('MQTT Publish to ', topic)
                data = json.dumps(door_dict).encode()
                mqtt_c.publish(topic, data, qos=0)
                mqtt_connected = True

            except Exception as e:
                print(e)
                gc.collect()
                mqtt_connected = False
    else:
        wlan.active(False)
        mqtt_connected = False

def task_mqttSubscribe():
    global nc
    global mqtt_c
    global mqtt_connected
    global mqtt_client_id
    topic=nc["topics"][1].encode()

    try:
        mqtt_c.check_msg()
    except:
        try:
            mqtt_c.connect()
            print('MQTT Subscribe to ', topic)
            mqtt_c.subscribe(topic)
            mqtt_connected = True
        except:
            print('MQTT Reconnect Failed')
            mqtt_connected = False

def lastwill():
    # update value before connection is dead due to power outage
    print("send last will message!")
    task_displayAllDoorInfo()
    task_mqttPublish()



# Main Program
if __name__ == '__main__':

    # Read configuration file (WLAN network, MQTT broker etc.)
    filename='network_config.json'
    with open(filename) as fp:
        nc = json.load(fp)

    # Initialize door's hardware and its dictionary (to store sensor data etc.)
    print("Initialize door...")
    door_dict = {}
    door = SecureDoor(lastwill_cb=lastwill)
    door.hwinit()

    # WLAN & MQTT
    wlan = network.WLAN(network.STA_IF)
    mqtt_client_id = ubinascii.hexlify(machine.unique_id())
    mqtt_c = MQTTClient(mqtt_client_id, nc["mqtt_broker"], port=nc["mqtt_port"], keepalive=nc["keepalive"])
    mqtt_c.set_callback(mqttSubscribeCallback)
    mqtt_connected = False

    # Task scheduler (function queue scheduler)
    # Less task ID -> Most Priority
    print("Create task & task scheduler")
    schd = FunctionQueueScheduler()
    t1 = FunctionQueueTask(task_fn=task_mqttSubscribe, task_id=1, scheduler=schd)
    t2 = FunctionQueueTask(task_fn=task_mqttPublish, task_id=2, scheduler=schd)
    t3 = FunctionQueueTask(task_fn=task_displayAllDoorInfo, task_id=3, scheduler=schd)
    t4 = FunctionQueueTask(task_fn=task_stepDoorState, task_id=4, scheduler=schd)
    schd.installTask(t1)
    schd.installTask(t2)
    schd.installTask(t3)
    schd.installTask(t4)

    # Set timer(s) for task trigger
    print("Initialize timer to trigger each tasks")
    tim1 = Timer()
    tim2 = Timer()
    tim3 = Timer()
    tim4 = Timer()
    tim1.init(period=17000, mode=Timer.PERIODIC, callback=t1.handler)
    tim2.init(period=15000, mode=Timer.PERIODIC, callback=t2.handler)
    tim3.init(period=5000, mode=Timer.PERIODIC, callback=t3.handler)
    tim4.init(period=2000, mode=Timer.PERIODIC, callback=t4.handler)
    wdt = WDT(timeout=8300)

    # Superloop
    # monitor watchdog and errors
    print("loop start!")
    while True:
        # task scheduler
        schd.popTask()
        time.sleep(0.5)

        # feed watchdog timer
        wdt.feed()

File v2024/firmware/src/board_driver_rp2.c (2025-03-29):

#include "board_driver_rp2.h"



// array of GPIO callback functions
static void (*gpio_cb[TOTAL_NUM_GPIO_RP2]) ();

// static vars for Timer
static struct repeating_timer t;
static uint32_t global_tick=0;

// ISR for GPIO
static void isr_gpio(uint gpio, uint32_t events) {
    gpio_cb[gpio]();
}

static bool isr_global_timer(struct repeating_timer *t) {
    global_tick++;
}

void driver_rp2_sysinit() {
    // Use printf as serial print on USB
    stdio_init_all();

    // setup clock speed
    /*
    clock_configure(clk_ref,
                    0,
                    0,
                    100 * MHZ,
                    100 * MHZ);
    */
}

void driver_rp2_set_gpio_input(uint8_t gpio_num, bool use_interrupt) {
    // Direction and pull-up setup
    gpio_set_function((unsigned char)gpio_num, GPIO_FUNC_SIO);
    gpio_set_dir(gpio_num, GPIO_IN);
    gpio_pull_up(gpio_num);
    
    // Enable an interrupt for target pin
    if (use_interrupt) {
        gpio_set_irq_enabled ((unsigned char)gpio_num, GPIO_IRQ_EDGE_FALL, true);
    }
}

void driver_rp2_enable_gpio_global_interrupt() {
    irq_set_enabled(IO_IRQ_BANK0, true);
    gpio_set_irq_callback (isr_gpio);
}

void driver_rp2_set_gpio_callback(uint8_t gpio_num, void (*cb) (void)) {
    gpio_cb[gpio_num] = cb;
}

bool driver_rp2_read_gpio(uint8_t gpio_num) {
    bool value;
    value = gpio_get(gpio_num);
    return value;
}

void driver_rp2_set_gpio_output(uint8_t gpio_num) {
    // Direction and pull-up setup
    gpio_set_function((unsigned char)gpio_num, GPIO_FUNC_SIO);
    gpio_set_dir((unsigned char)gpio_num, GPIO_OUT);
    gpio_disable_pulls((unsigned char)gpio_num);
}

void driver_rp2_write_gpio(uint8_t gpio_num, bool value) {
    gpio_put((unsigned char)gpio_num, value);
}

void driver_rp2_create_global_tick(uint32_t tick_period_ms) {
    add_repeating_timer_ms(tick_period_ms, isr_global_timer, NULL, &t);
}

uint32_t driver_rp2_get_global_tick() {
    return global_tick;
}

int driver_rp2_enable_wifi() {
    uint8_t timeout=WIFI_INIT_TIMEOUT;
    while (cyw43_arch_init() && (timeout > 0)) {
        sleep_ms(1000);
        timeout--;
    }
    if (timeout == 0) {
        return -1;
    }
    else {
        cyw43_arch_enable_sta_mode();
        return 0;
    }
}

int driver_rp2_connect_to_wifi(const char *ssid, const char *pwd, uint32_t timeout) {
    return cyw43_arch_wifi_connect_timeout_ms(ssid, pwd, CYW43_AUTH_WPA2_AES_PSK, timeout);
}

bool driver_rp2_is_wifi_connected() {
    if (cyw43_wifi_link_status (&cyw43_state, CYW43_ITF_STA) == CYW43_LINK_JOIN) {
        return true;
    }
    else {
        return false;
    }
}

void driver_rp2_watchdog_enable(uint32_t delay_ms) {
    watchdog_enable(delay_ms, false);
}

void driver_rp2_watchdog_feed() {
    watchdog_update();
}

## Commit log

2024-02-03 rp2, activate exit button even in IDLE state
2024-02-03 rp2, add buzzer for alarm when outage is occured
    [secure_doorlock.py]
2024-02-09 rp2, add lastwill before go to ACTIVE state when outage occur + buzzer fadeout
    [main.py, secure_doorlock.py]
2024-03-21 worker, use logging.info() instead of print()
2025-02-26 add firmware folder for rp2 failsecure controller
    [main_app.c]
2025-03-10 firmware, add app button
2025-03-10 firmware, add app LED
2025-03-10 firmware, add driver layer for rp2040
2025-03-11 firmware, add app for boltlock dsk4t100
2025-03-11 firmware, fix GPIO interrupt bug from NULL fn pointer
    [app_button.c, app_dsk4t100.c, board_driver_rp2.c]
2025-03-12 firmware, update driver
2025-03-17 firmware, update rp2 driver by adding WiFi and WDT
2025-03-29 firmware, add lock/unlock pin and change release process
2025-03-29 firmware, update app_accessctrl for exit button in slidedoor
2025-03-30 firmware, fix the reversed logic of door status
    [app_dsk4t100.c]
2025-04-18 add KiCAD pcb files of v2024
    [FailSecure_DS-K4T100.kicad_pcb, FailSecure_DS-K4T100.kicad_sch]
2025-11-09 Kicad, add a new parts from JLCPCB
2025-11-09 Kicad, update schematic for access control v2025
    [FailSecure_DS-K4T100.kicad_sch]
2025-11-09 Kicad, update PCB layout for a new schematic
    [FailSecure_DS-K4T100.kicad_pcb, FailSecure_DS-K4T100.kicad_sch]
2025-11-10 Kicad, move 2x5 connector to fit inside the board
    [FailSecure_DS-K4T100.kicad_pcb]
2025-11-10 update PCB silkscreen
    [FailSecure_DS-K4T100.kicad_pcb]
2025-11-10 Kicad, add LCSC part number to forgotten devices & Don't populate jumper
    [FailSecure_DS-K4T100.kicad_pcb, FailSecure_DS-K4T100.kicad_sch]
2025-11-10 Update BOM by remove extended part as much as posible
    [FailSecure_DS-K4T100.kicad_pcb, FailSecure_DS-K4T100.kicad_sch]
